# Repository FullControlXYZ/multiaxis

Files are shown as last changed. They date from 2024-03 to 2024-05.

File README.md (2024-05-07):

# multiaxis

### follow **[THIS GUIDANCE DOCUMENT](https://colab.research.google.com/github/FullControlXYZ/multiaxis/blob/main/prusai3_XYZB1/prusa_4axis_guide_colab.ipynb)** to convert a prusa i3 to a 4-axis printer **AND** use [FullControl](https://github.com/FullControlXYZ/fullcontrol/#readme) to generate 4-axis gcode directly within the guide!

A 5-axis addon is described [here](https://github.com/FullControlXYZ/multiaxis/tree/main/prusai3_XYZB1C0#readme)

<p align="center">
  <picture>
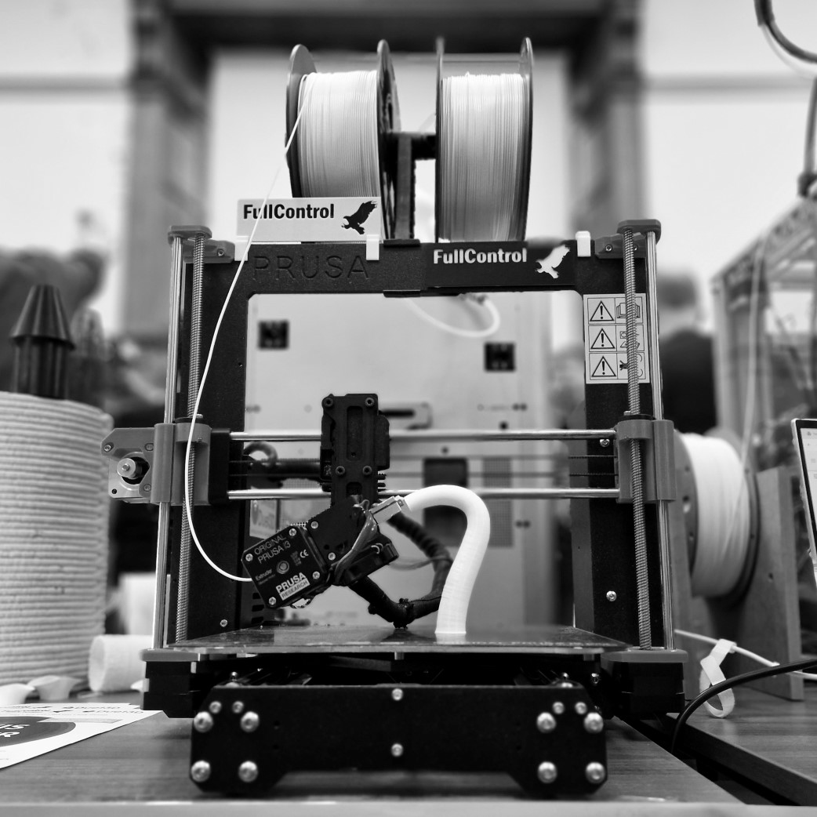
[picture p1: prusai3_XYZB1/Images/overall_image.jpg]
  
  </picture>
  <br><b>think beyond <em>'normal'</em> 3D printing</b><br><br>
</p>

------------------

repo information:

open-source multiaxis 3D printing capabilities developed as part of [FullControl research](https://github.com/FullControlXYZ/fullcontrol/#readme) with support from [Duet3D](https://www.duet3d.com/) and undertaken by engineering students (Renush Vigneswaran and Nathanael Hogg) at [Loughborough University](https://www.lboro.ac.uk/)

if you follow the guide, please let us know :) ... email [info@fullcontrol.xyz](mailto:info@fullcontrol.xyz)

it links to 5-axis and multi-tool revisions of the 4-axis version

multiaxis toolpath design demos are provided in [FullControl documentation](https://github.com/FullControlXYZ/fullcontrol/#readme)

current naming convention (may change in the future):

- X Y Z [i][0/1] [ii][0/1] ...
    - i/ii/... = rotation axes (X=A, Y=B, Z=C)
    - 0/1 indicates whether the stated axis rotates the print-platform/tool respectively
    - axes are listed in the order: X then Y then Z (omit X/Y/Z if not present) then print-platform-rotation axes (0-axes), then tool-rotation axes (1-axes)
        - for multiple directly connected rotation axes, a sequence of parent-child dependency is used: a rotating print-platform (C0) attached onto a tilting stage (A0) would be A0C0 (C is dependent on A)

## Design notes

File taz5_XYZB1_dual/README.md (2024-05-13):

follow the **[PRUSA_i3 GUIDANCE DOCUMENT](https://colab.research.google.com/github/FullControlXYZ/multiaxis/blob/main/prusai3_XYZB1/prusa_4axis_guide_colab.ipynb)** as much as possible

changes from that document:
- print stl files from [here](https://github.com/FullControlXYZ/multiaxis/tree/main/taz5_XYZB1_dual/CAD)
    - (step files are [here](https://github.com/FullControlXYZ/multiaxis/tree/main/taz5_XYZB1_dual/CAD/STEP)) - adjust them for the geometry of the extruders you use
- different re-wiring procedure
    - this [duet wiring doc](https://github.com/FullControlXYZ/multiaxis/tree/main/taz5_XYZB1_dual/Duet%20Wiring) is a useful reference
    - also check duet guidance doc ([example](https://docs.duet3d.com/How_to_guides/e3p_Mini5+_guide_part1_wiring))
- changes to duet configuration files - [updated version available here](https://github.com/FullControlXYZ/multiaxis/tree/main/taz5_XYZB1_dual/Config%20Files)
- an example fullcontrol design is [here](https://colab.research.google.com/github/FullControlXYZ/multiaxis/blob/main/taz5_XYZB1_dual/demo.ipynb)
- we used a [100:1 gearbox-motor combo](https://www.active-robots.com/3322-0-28sth32-nema-11-bipolar-stepper-with-100-1.html?amp=1), more precise than 27:1, but this meant we needed backlash compensation in the toolpath
- anything else? let us know!

email: [info@fullcontrol.xyz](mailto:info@fullcontrol.xyz)

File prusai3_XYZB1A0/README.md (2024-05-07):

guidance for this is upcoming, but it's very simple... 

- follow the [rotating-bed 5-axis guide](https://github.com/FullControlXYZ/multiaxis/tree/main/prusai3_XYZB1C0/#readme)
- reorient the 5th axis so the rotation happens about X instead of Z - good for printing on a mandrel or other parts
- maybe no modifications to config.g (to be confirmed) - all inverse kinematics are handled by FullControl
- change the manual homing routine (set all axes to the zero when the nozzle tip is in line with the mandrel axis, at a logical X)
- change settings used in FullControl for inverse kinematics

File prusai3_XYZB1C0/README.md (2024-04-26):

follow the **[PRUSA_i3 GUIDANCE DOCUMENT](https://colab.research.google.com/github/FullControlXYZ/multiaxis/blob/main/prusai3_XYZB1/prusa_4axis_guide_colab.ipynb)** with the following additions:

- print the additional stl files from [here](https://github.com/FullControlXYZ/multiaxis/tree/main/prusai3_XYZB1C0/CAD)
- wire in the new motor ('C' in this image):
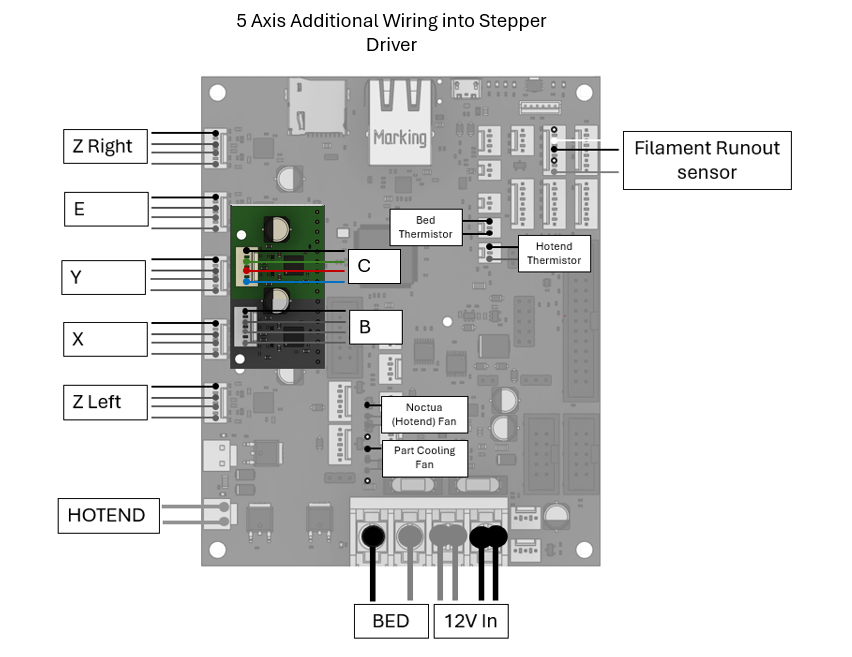
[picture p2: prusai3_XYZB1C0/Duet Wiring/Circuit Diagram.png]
    
- implement minor changes to config file described in the 'Changes to config' section below (updated config file available [here](https://github.com/FullControlXYZ/multiaxis/blob/main/prusai3_XYZB1C0/prusai3_XYZB1C0/Config%20Files/))
- Follow the '5-axis manual homing routine' instructions below
- anything missing from these instructions? let us know! [info@fullcontrol.xyz](mailto:info@fullcontrol.xyz)

## Changes to config:

By utilising the same motor as the 4th axis, the method to add any additional axis in any orientation requires very few changes to config.g:
- Define the extra drive and update the mapping command in the “ ##### Drives” section (changes highlighted in bold): 
    - **M569 P6 S0 D3 V10 		        ; C drive @6**
    - M584 X1 Y2 Z0:4 E3 B5 **C6**                            ; set drive mapping
- Set motor parameters (changes highlighted in bold): 
    - M350 X16 Y16 Z16 E16 B16 **C16** I1  ; configure microstepping with interpolation
    - M92 X100.00 Y100.00 Z400.00 E140.00 B238.6776859 **C238.6776859**    ; set steps per mm 
    - M566 X600.00 Y600.00 Z48.00 E300.00 B480 **C480**      ; set maximum instantaneous speed changes (mm/min)
    - M203 X8000.00 Y8000.00 Z720.00 E7200.00 B5000.00 **C5000.00**    ; set maximum speeds (mm/min)
    - M201 X1250.00 Y1250.00 Z1250.00 E2000.00 B1000.00 **C1000.00** ; set accelerations (mm/s^2)
    - M906 X750 Y750 Z600 E700 B600 **C600** I30                  ; set motor currents (mA) and motor idle factor in per cent
- Update the axis limits:
    - Original (4-axis):
        - M208 X0:200 Y0:210 Z0:200 B-90:90             ; set axis minima and maxima
    - Updated:
        - **M208 X-100:100 Y-105:105 Z-50:40 B-90:90 C-999999:999999**             ; set axis minima and maxima

## 5-axis manual homing routine:

Manually home axes (to be automated in the future):
1. Place 5th axis motor bracket on the print bed :
    - Whilst this could be anywhere on the print bed, depending on the design, it is recommended to leave at centre (The axes limits have been set assuming central position)

1. Home B:
    - Use Duet Web Control to jog B until nozzle points directly down 

1. Position Nozzle to be at the centre of the rotating bed (an indentation is designed into bed to clearly indicate centre):
    - Use Duet Web Control to jog X, Y and Z until the nozzle pinches paper at the centre of the bed.
    - Note down X Y (anmd maybe Z) values to easily move to this position for subsequent homing.

1.	Set home for all axis: G92 Z0 X0 Y0 B0 C0 

1. Begin printing, following these steps:
    1.	Click T0 in duet web control and set nozzle temperature and bed temperature
    1.	Load gcode file (without start/end-procedures except M82/M83) onto printer
    1.	Run gcode file (use very slow speeds if you have no cooling fan)

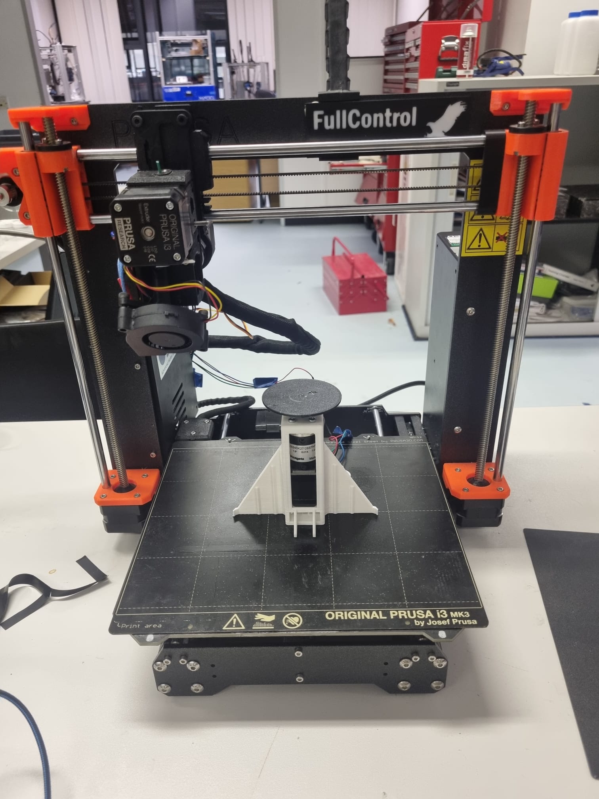
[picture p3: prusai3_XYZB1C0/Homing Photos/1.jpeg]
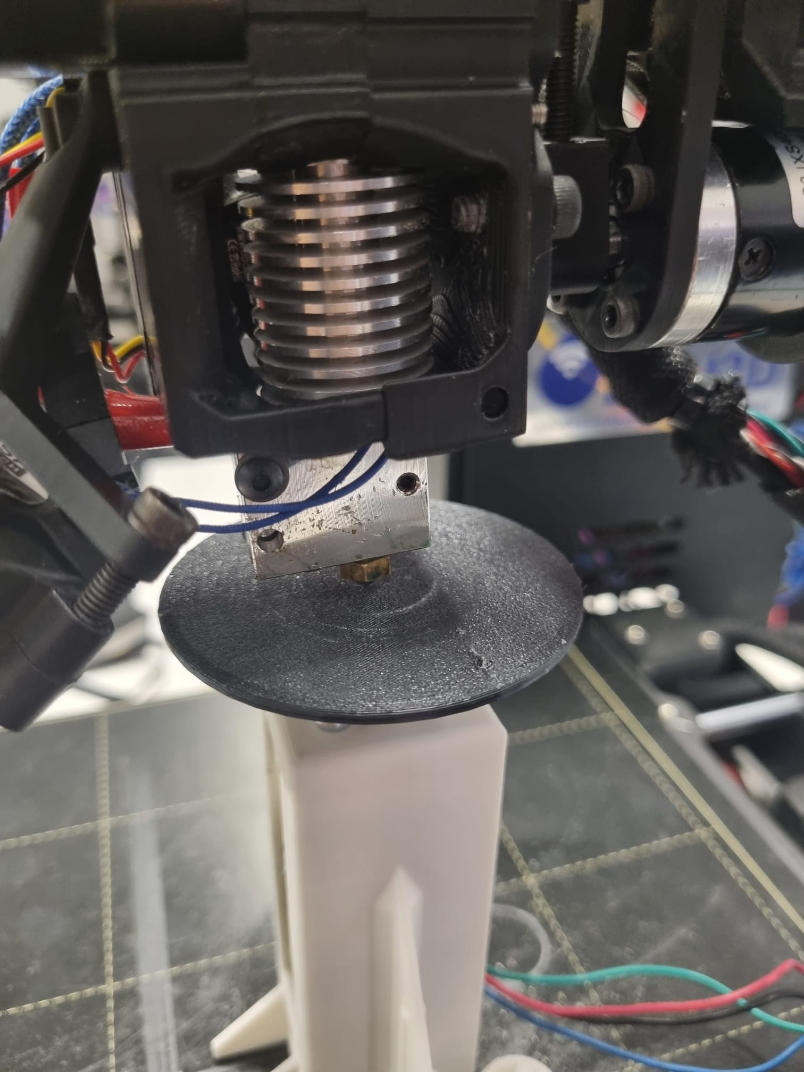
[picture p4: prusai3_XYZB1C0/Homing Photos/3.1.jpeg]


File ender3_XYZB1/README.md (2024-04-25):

follow the **[PRUSA_i3 GUIDANCE DOCUMENT](https://colab.research.google.com/github/FullControlXYZ/multiaxis/blob/main/prusai3_XYZB1/prusa_4axis_guide_colab.ipynb)** as much as possible

changes from that document:
- print stl files from [here](https://github.com/FullControlXYZ/multiaxis/tree/main/ender3_XYZB1/CAD) instead of the three prusa brackets
    - these are untested and may need minor modifications (step files are [here](https://github.com/FullControlXYZ/multiaxis/tree/main/ender3_XYZB1/CAD/STEP)) - please give feedback and help develop this work!
- you no longer need the Duet 3 Mini 2+ expansion board since there is only one Z-axis motor (it is required for the prusa because it has two Z motors)
    - note: you may wish to use one anyway, to be able to update to 5-axis in the future
- minor changes to wiring
    - this [ender 3 pro guidance doc](https://docs.duet3d.com/How_to_guides/e3p_Mini5+_guide_part1_wiring) may be a useful reference
- minor changes to config file (only one motor for Z axis)
- anything else? let us know!

email: [info@fullcontrol.xyz](mailto:info@fullcontrol.xyz)

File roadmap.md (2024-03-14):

immediate:
1. add endstops and automated homing guidance
1. add part cooling guidance
    1. options: existing fan / aquarium pump
1. add brackets for alternative printers
1. add a 5th axis (rotating bed and mandrel options)
1. turret tool!!! (multiple print heads and inspection tools 'activated' simply by rotation of the B axis)

maybe:
1. remove bracket supporting the back of the motor by increasing rigity of the front bracket
1. try a [more widely available](https://thepihut.com/products/bipolar-stepper-motor-with-planet-gear-box-18kg-cm) motor-gearbox combo but lower gear ratio (is microstepping enough?)

next:
1. templates/guides for community contribution
1. further demos and docs for automated 4- and 5-axis toolpath generation with FullControl
    - combine with stl import... still not 'slicing' but using geometric data in a range of ways
1. conversions that can utilise the existing controller board for printers
1. conversions of non-bed-slinger printers

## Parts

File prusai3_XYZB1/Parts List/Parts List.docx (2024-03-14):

Parts | Quantity | Source
Nema 11 Stepper Motor with 27:1 Gearbox | x1 | https://www.active-robots.com/3321-0-28sth32-nema-11-bipolar-stepper-with-27-1-gearbox.html
Duet 3 Mini 5+ | X1 | https://www.duet3d.com/duet3mini5plus
Duet 3 mini 2+ | X1 | https://www.duet3d.com/duet3expansionmini2plus
Extruder Bracket | X1 | Print STL files available here: https://github.com/FullControlXYZ/media/tree/main/4_axis_docs/CAD
Motor Bracket Front | X1
Motor Bracket Rear | X1
Duet Case | X1
Duet Case Lid | X1
Hotend Cover | X1 - Optional
M3x10 | X11
M3 Nut | X1
M4x10 | X6
M4x40 | X2
M4x25 | X1
M4x6 | X1

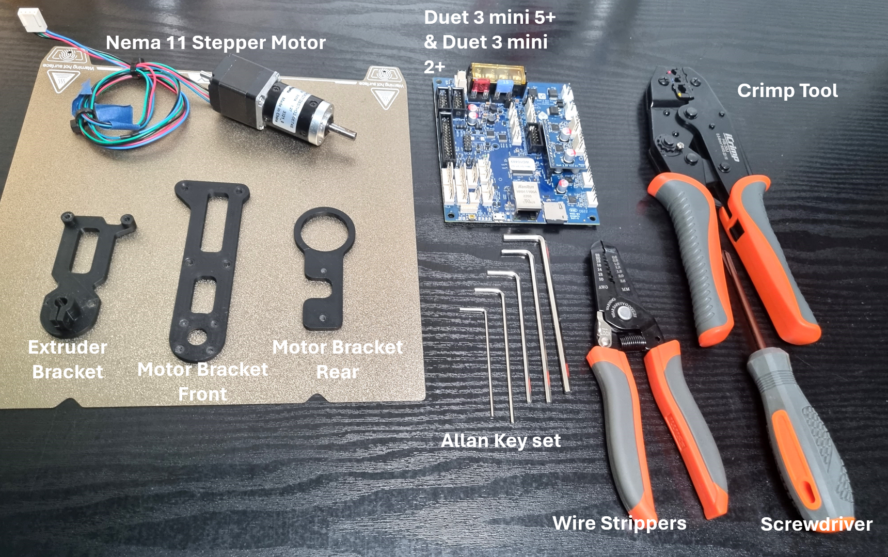
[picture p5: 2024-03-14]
prusai3_XYZB1/Parts List/Basic Parts.png

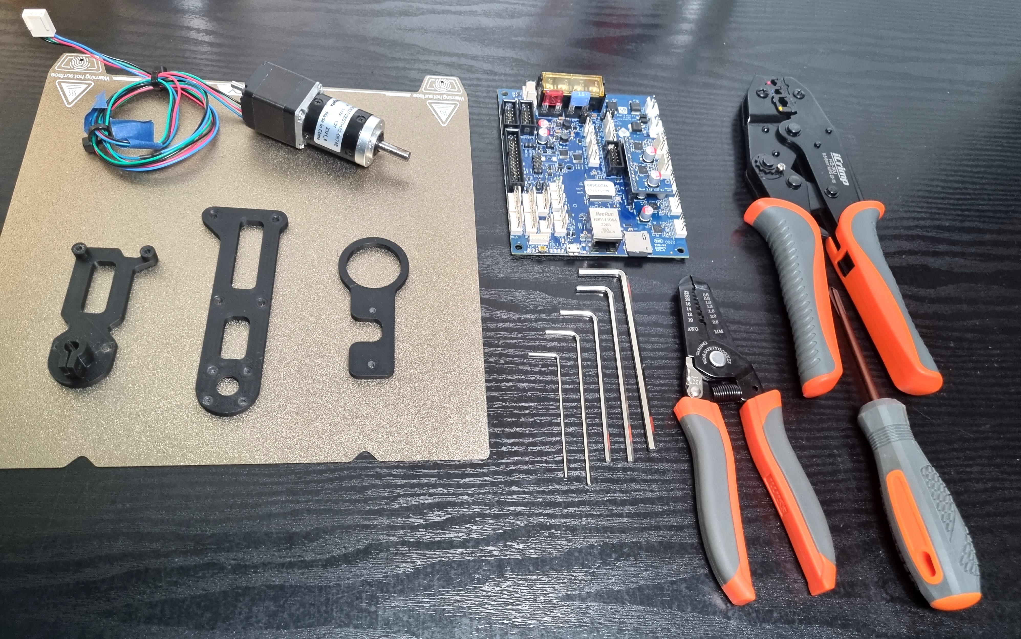
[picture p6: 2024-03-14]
prusai3_XYZB1/Parts List/Parts Image.jpg

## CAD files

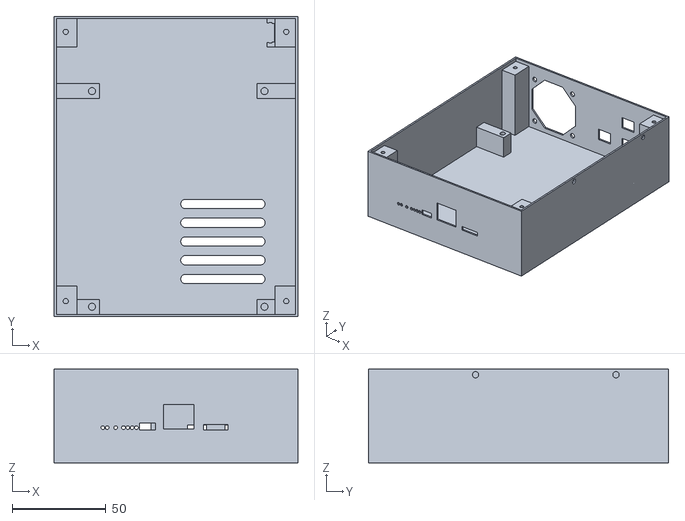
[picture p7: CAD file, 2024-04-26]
prusai3_XYZB1/CAD/Optional/Duet Case.stl
130.0 x 160.0 x 50.0

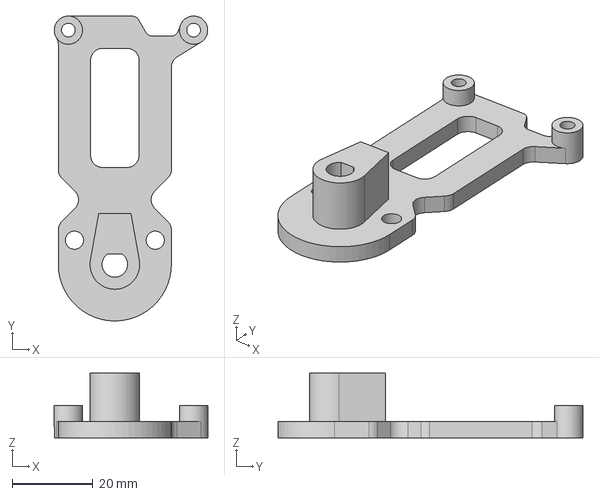
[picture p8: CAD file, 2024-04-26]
prusai3_XYZB1/CAD/step/Extruder Bracket.step
38.0 x 75.5 x 16.0 mm

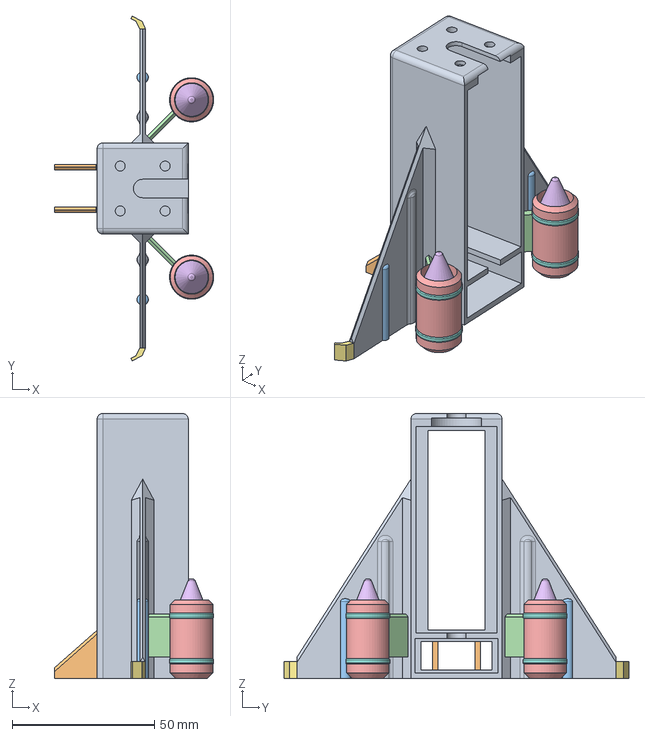
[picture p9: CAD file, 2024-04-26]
prusai3_XYZB1C0/CAD/STEP/Motor Bracket.stp
55.9 x 121.0 x 93.0 mm

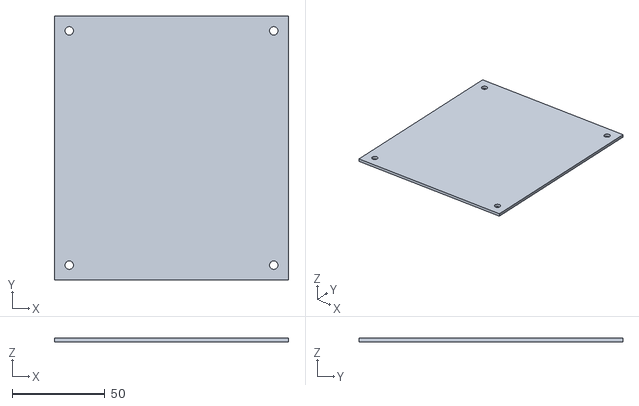
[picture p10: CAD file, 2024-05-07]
taz5_XYZB1_dual/CAD/DuetEnclosureLid.stl
126.0 x 142.0 x 2.00

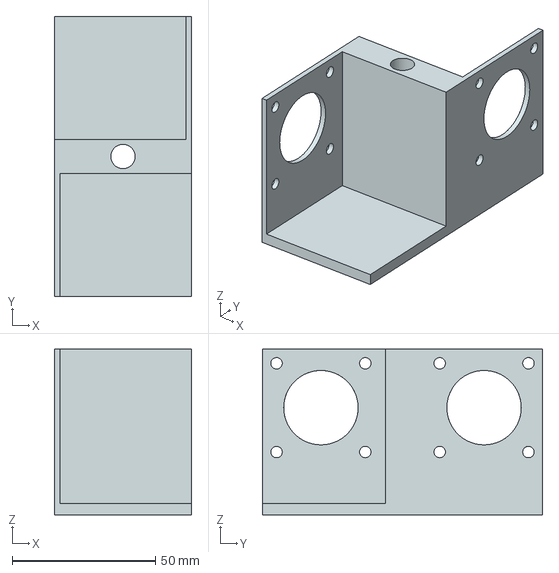
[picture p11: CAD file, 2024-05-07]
taz5_XYZB1_dual/CAD/Step/ExtruderMount.stp
48.0 x 98.0 x 58.0 mm

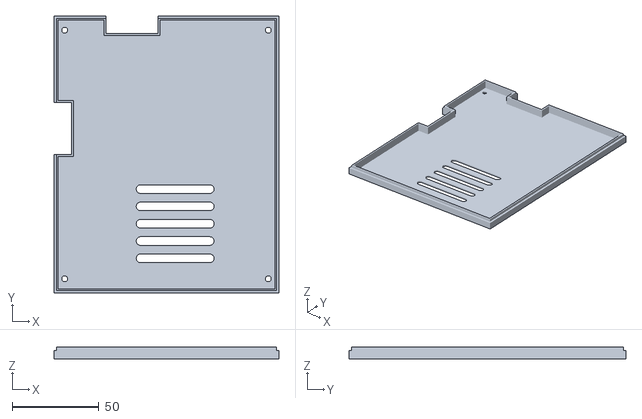
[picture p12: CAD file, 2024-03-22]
prusai3_XYZB1/CAD/Optional/Duet Case Lid.stl
130.0 x 160.0 x 6.99

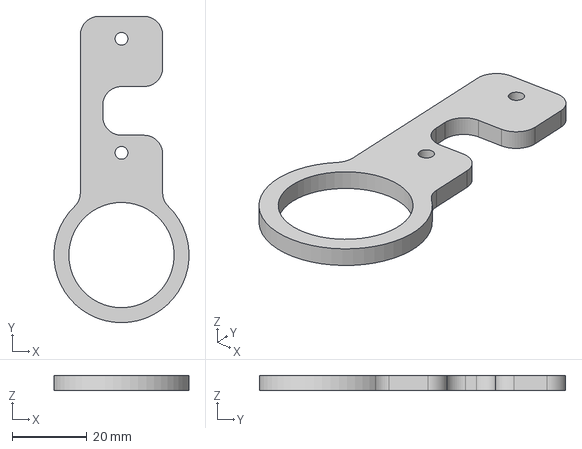
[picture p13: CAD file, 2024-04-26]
prusai3_XYZB1/CAD/step/Motor Bracket Rear.step
36.0 x 81.8 x 4.00 mm

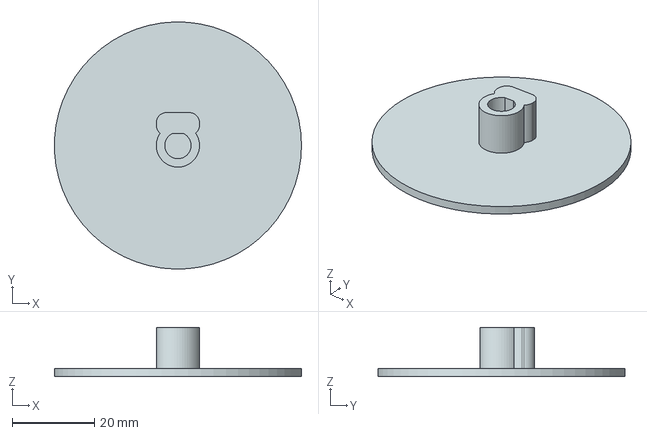
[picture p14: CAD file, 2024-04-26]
prusai3_XYZB1C0/CAD/STEP/Rotating Bed.stp
60.0 x 60.0 x 12.0 mm

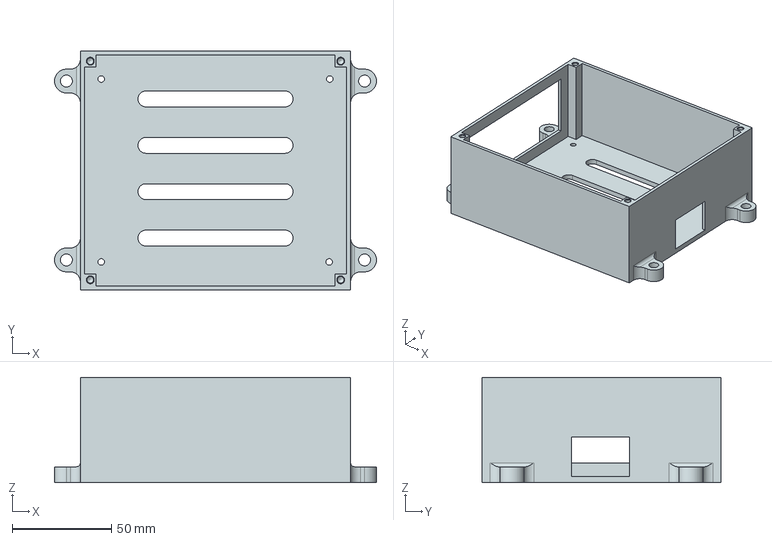
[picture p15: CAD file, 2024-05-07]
taz5_XYZB1_dual/CAD/Step/DuetEnclosure.stp
162.0 x 120.0 x 53.0 mm

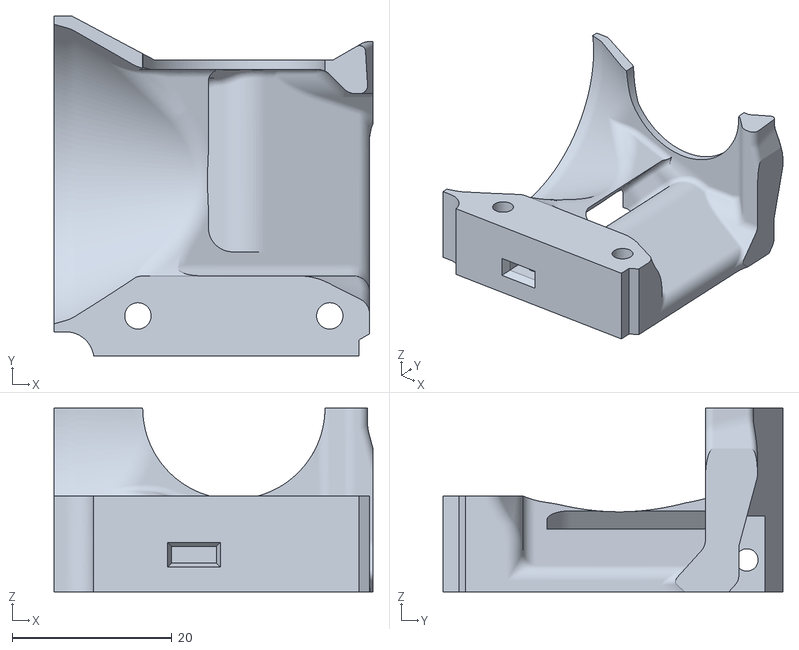
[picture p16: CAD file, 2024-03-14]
prusai3_XYZB1/CAD/Optional/Hotend Cover.stl
39.9 x 42.5 x 23.0

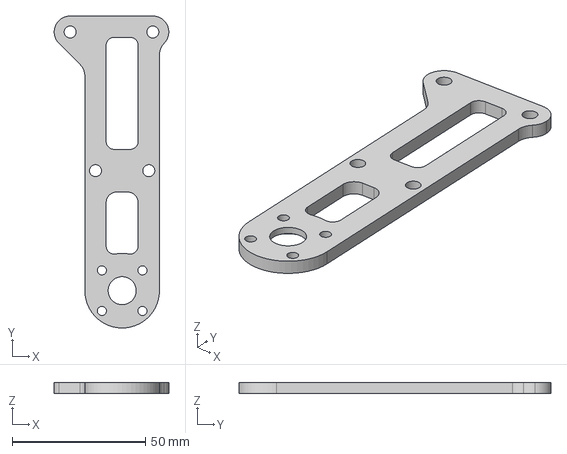
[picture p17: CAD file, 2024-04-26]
prusai3_XYZB1/CAD/step/Motor Bracket Front.step
43.0 x 117.0 x 4.00 mm

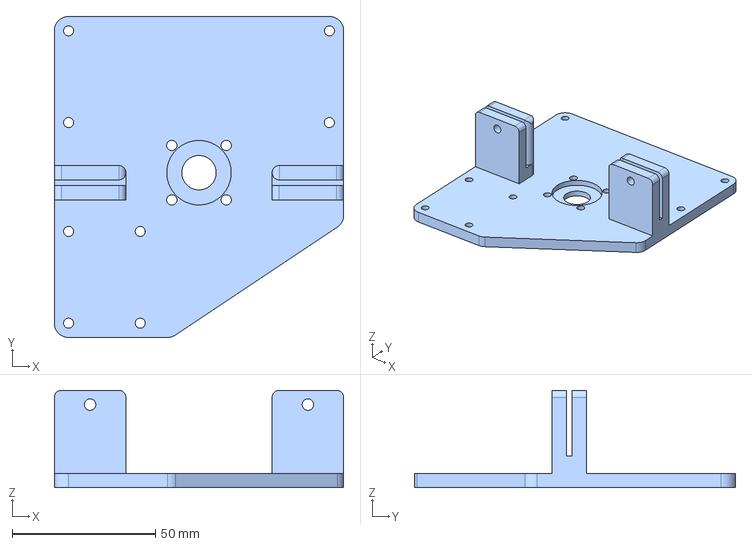
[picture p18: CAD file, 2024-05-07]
taz5_XYZB1_dual/CAD/Step/Backplate.stp
101.0 x 112.0 x 34.0 mm

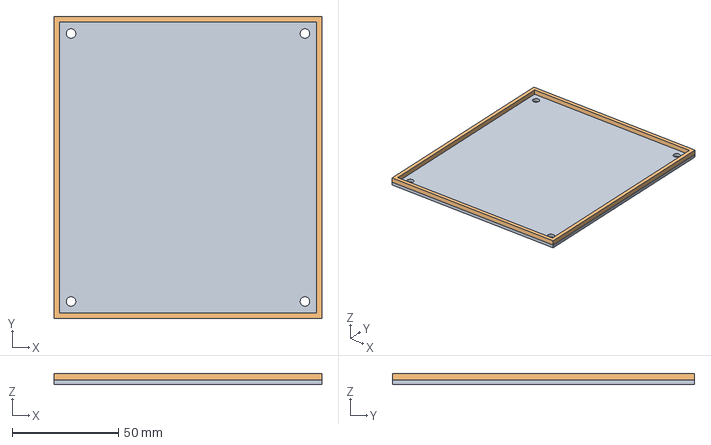
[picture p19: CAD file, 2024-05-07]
taz5_XYZB1_dual/CAD/Step/DuetEnclosureLid.prt.stp
126.0 x 142.0 x 5.00 mm

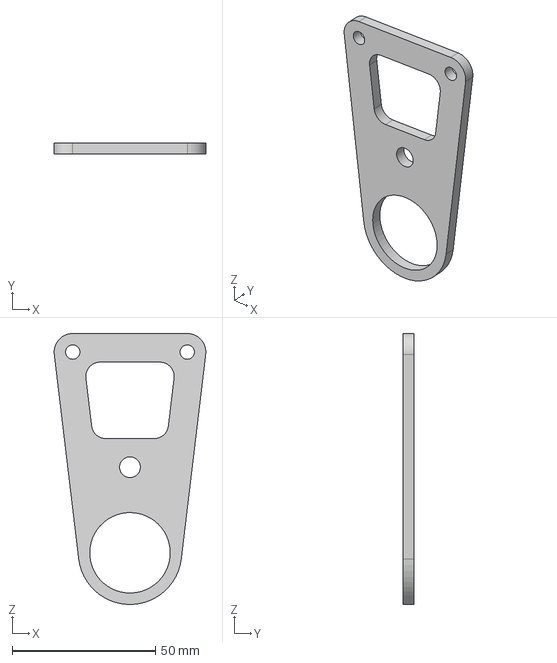
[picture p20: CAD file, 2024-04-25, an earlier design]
ender3_XYZB1/CAD/STEP/Motor Bracket Rear.step
53.0 x 4.00 x 94.7 mm

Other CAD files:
prusai3_XYZB1/CAD/Old/Motor Bracket Rear v01.stl
ender3_XYZB1/CAD/STEP/Motor Bracket Front.step
prusai3_XYZB1/CAD/Old/Extruder Bracket v01.stl
ender3_XYZB1/CAD/STEP/Extruder Bracket.step
ender3_XYZB1/CAD/Extruder Bracket.stl
ender3_XYZB1/CAD/Motor Bracket Front.stl
ender3_XYZB1/CAD/Motor Bracket Rear.stl
prusai3_XYZB1/CAD/Extruder Bracket.stl
prusai3_XYZB1/CAD/Motor Bracket Front.stl
prusai3_XYZB1/CAD/Motor Bracket Rear.stl
prusai3_XYZB1/CAD/Old/Motor Bracket Front v01.stl
prusai3_XYZB1C0/CAD/STL/Motor Bracket.stl
prusai3_XYZB1C0/CAD/STL/Rotating Bed.stl
taz5_XYZB1_dual/CAD/Backplate.stl
taz5_XYZB1_dual/CAD/DuetEnclosure.stl
taz5_XYZB1_dual/CAD/ExtruderMount.stl

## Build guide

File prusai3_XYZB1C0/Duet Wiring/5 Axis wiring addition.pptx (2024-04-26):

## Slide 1

5 Axis Additional Wiring into Stepper Driver

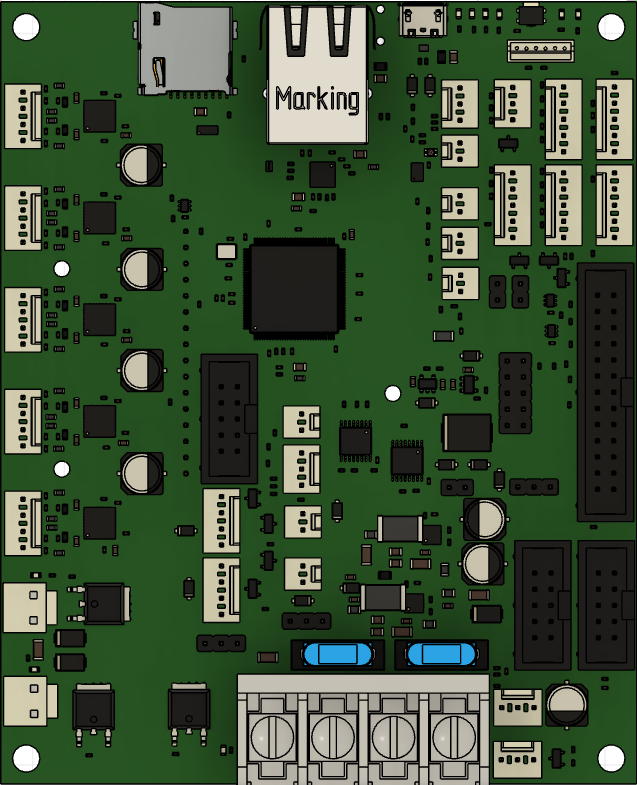
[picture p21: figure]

Z Right

Filament Runout sensor

E

Y

Bed Thermistor

Hotend Thermistor

X

Z Left

HOTEND

BED

12V In

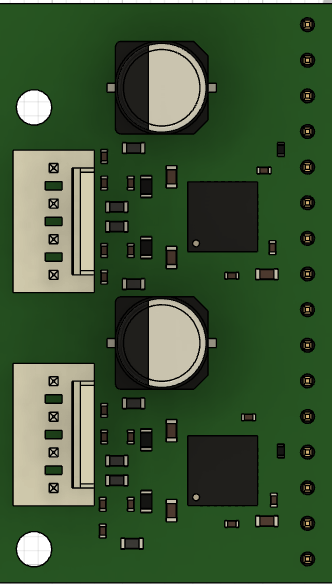
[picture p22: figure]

B

C

Noctua (Hotend) Fan

Part Cooling Fan

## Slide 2

5 Axis Additional Wiring into Stepper Driver

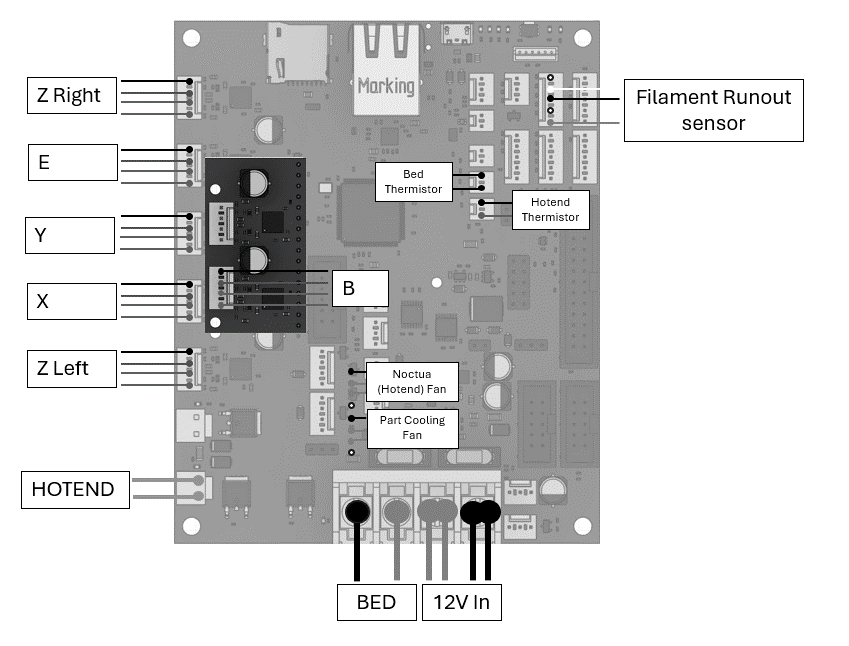
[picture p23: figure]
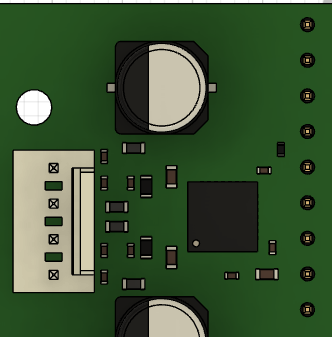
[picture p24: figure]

C

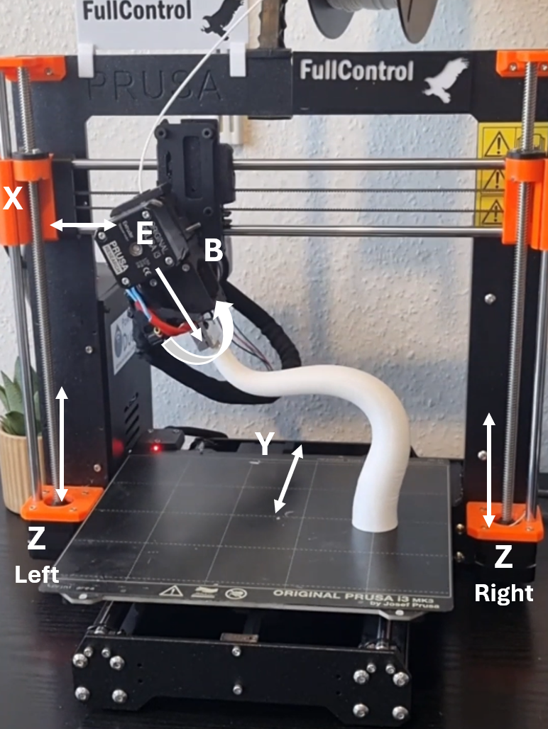
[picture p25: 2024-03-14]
prusai3_XYZB1/Images/Printer Axis Labelled.png

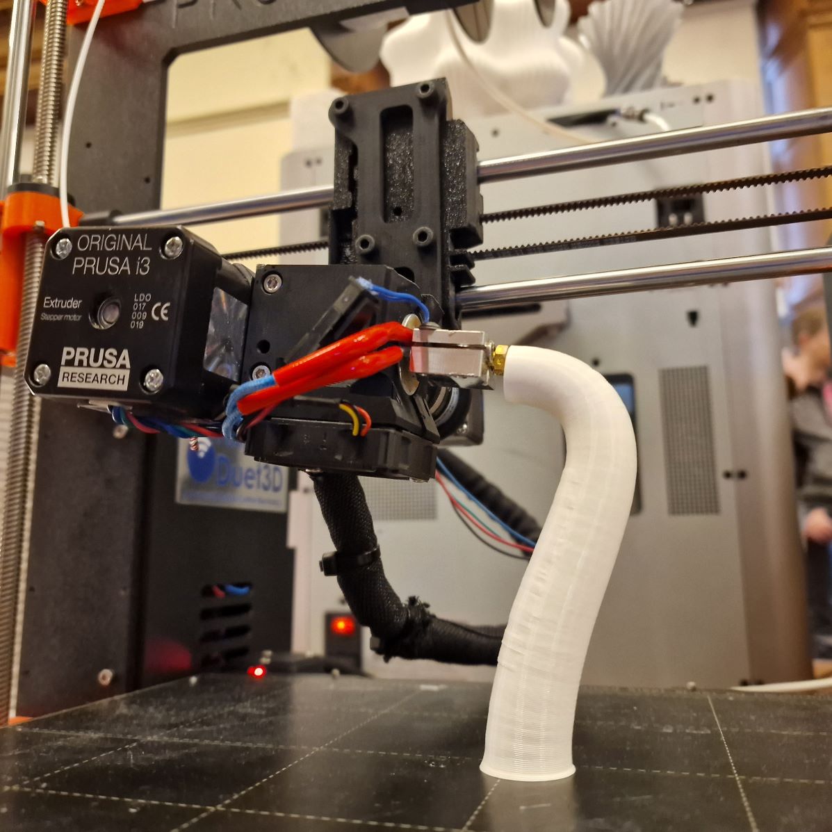
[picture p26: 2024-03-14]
prusai3_XYZB1/Images/zoomed_printing_image.jpg

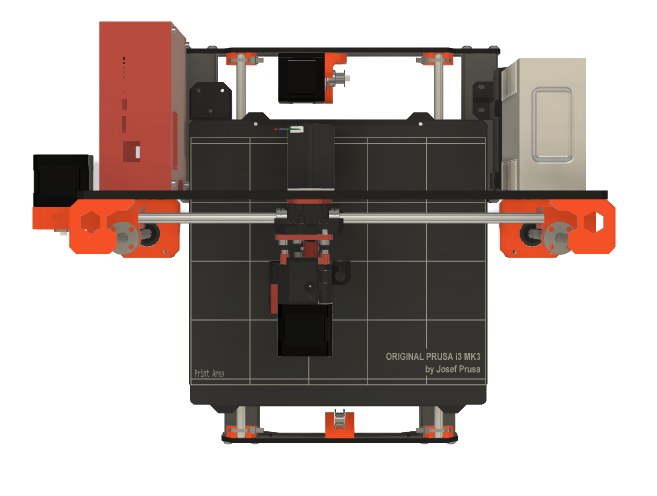
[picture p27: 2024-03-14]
prusai3_XYZB1/Exploded View/Assembled Birdseye View.png

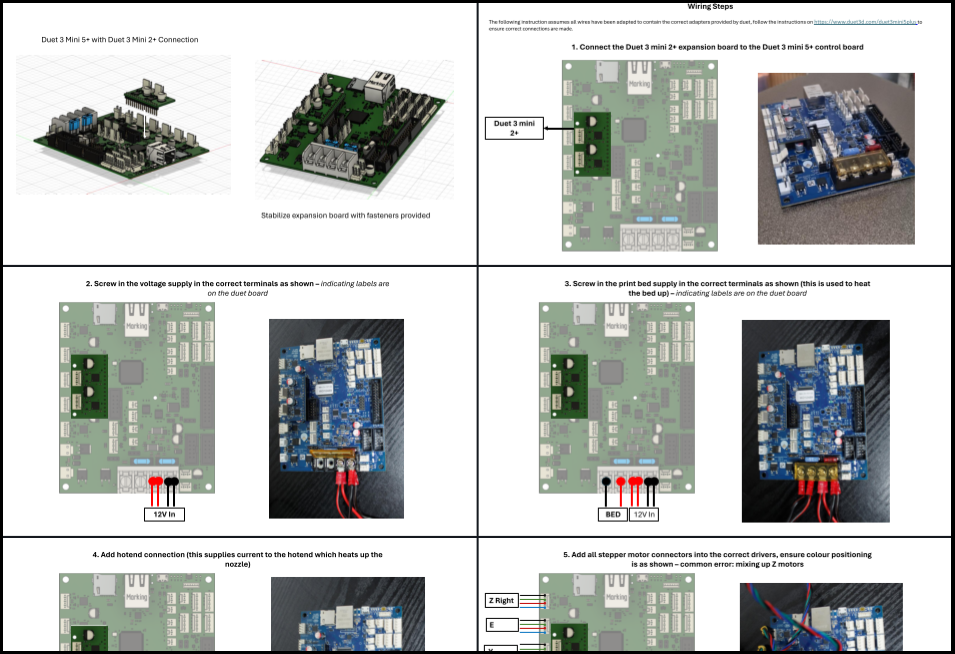
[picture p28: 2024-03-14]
prusai3_XYZB1/Duet Wiring/Screenshot.png

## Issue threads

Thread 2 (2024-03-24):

Adding a new rotary axis!

Fisherm2, 2024-03-24:
I am very interested in your 4-axis printer, I would like to make a similar 5-axis printer, and the difference with your project is that I try to add two rotary axes in the print head, is there any related firmware support or tutorial document, thank you very much!

fullcontrol-xyz, 2024-03-30:
This isn't something I've previously done but it will be supported by FullControl! And the firmware will handle it easily as long as FullControl (or some equivalent software) does the inverse kinematics. Let us know when you are close to a working system and we can get the kinematics sorted out if it isn't already built in to FullControl by that time. Sorry for the slow reply... I accidently didn't have notifications set up for this repo 🤦

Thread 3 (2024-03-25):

Motor Bracket Front Hole Alignment Issue

NealParkhurst, 2024-03-25:
Firstly, huge congrats on a fabulous project!

When assembling the Motor Bracket Front to the gearbox I found that it was tricky to get the fixing holes lined up and was concerned that I might cross thread / damage the threads. As the gearbox is already concentrically aligned by the step detail in the bracket you could increase the diameter of the fixing thru holes to eliminate this issue. Cheers, Neal

fullcontrol-xyz, 2024-03-30:
Thanks very much for letting us know. Sorry for the slow reply. I didn't have alerts set on for issues for some reason. We'll sorting out larger holes. We're also working on some slightly updated brackets. So will make sure they feature in them

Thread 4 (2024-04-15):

3d printers compatibility

Prumnea, 2024-04-15:
I have read your work on converting the Prusa MK3S to have a 4th-axis printer. That is really impressive!
 I would like to ask if other types of Prusa printers or printers from other brands would work as well?

Regards,
Prumnea

fullcontrol-xyz, 2024-04-15:
Thanks very much!

Yep it will work in basically an identical manner for any other printer that you convert to run off the duet controller.

There may be some small changes to the firmware required (e.g. if there is only one motor for the z axis instead of two), but if there are any changes required, they will be minor and you can ask on here for help.

There will also potentially need to be some changes to the brackets. I'm not sure how the x-carriages vary from prusa to prusa. This would involve designing a revised bracket with new hole positions. It's an easy CAD job. We've provided the step files for our models.

We're already looking at releasing brackets for an ender 3. If anyone creates new brackets for alternative printers, please let us know and we'll add them to this repo and the guide so other people can benefit!

Andy

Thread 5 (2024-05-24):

Using an alternative controller board

fullcontrol-xyz, 2024-05-24:
Questions by email:

Hello, I am currently following your mod for the 4th axis for the prusa and I have few questions.
1. any board that works on reprap with more than 6 steppers should work? XY2ZEB considering that the board I am thinking to use is having 7 steppers, i am currently can't get my hands on the duet mini 5+ because it is really expensive to get in my country, and importing it myself will be expensive as well.
2. there is any alternative for the nema11 with gearbox? as far I understand you want to use nema11 for it light weight uses and the gearbox to get higher torque?
I can't somehow get my hands on it and thought maybe I could get my hands on different one?
I can order this from amazon but it will take well over a month to arrive.
3. at the demo design I really didn't understand what is the "Nozzle_Tip_axis_offset" mean if you could have a simple explanation for this is will be great.
4. Can I get the whole step files for the project with the printer included? In case I would want to fit stuff to it on the github there is a step only for the printed parts.
And thank you again for your amazing work, can't wait to start building this.

fullcontrol-xyz, 2024-05-24:
Response:

That’s really cool to hear you’re following the instructions.
In response to your questions:
1.	It should yes, but you’ll need to modify the firmware yourself (please share your firmware and board details if you do! – we’ll add it to the github repo)
2.	You can try an alternative gearbox/motor for sure. We got a 100:1 gearbox version of the one we link to (27:1) and it worked, but introduced backlash, for which we needed to compensate in FullControl. So I’d go for a gear ratio of perhaps 10-50 and see how it goes. Weight is the main consideration yeh.
3.	Nozzle tip axis offset is the distance the nozzle is below the axis of rotation (B axis). This is important because when rotate the toolhead, the distance of the nozzle tip from the axis of rotation dictates how much the nozzle moves.
4.	I’ll ask my student to send the printer step files.

AssafKatan, 2024-05-24:
Hello, thank you for answer!
This is assaf Whom sent the email.
1. I got my self a Mellow E3 RRF board, it does have enough stepper drivers to work with 4 axis for now this will be enough, I will consider getting a duet board if there will be an integration of 5th axis by you guys or rather by me if I will find it possible.(Considering the price of the duet boards this was a easy buy for me just to test the concept).

2. I found myself a motor that will fit the original design, I could find a seller on aliexpress that sold me a nema11 27:1 motor that should just fit in the design, if not I will make some changes to make it fit.

I have got myself a Prusa clone just beacuse I thought that assembling it on a original prusa is hurtful lol, considering they are pretty expensive in my country and I could find the clone for less than a half price so it will be good for testing this.
I will update in this thread about my work using the different board.

3-4 Thank you!! this is really helpful, and releasing this project as open source is amazing and I am really happy about it, I am 7 years into printing and always wanted to try more than the normal "2.5D" printing.

fullcontrol-xyz, 2024-06-03:
All sounds good! Let us know any progress, if you need to make changes to any of the brackets keep good records along with any other necessary deviations from the guidance doc. Then we'll be able to quickly write a custom guide for your printer and controller, which only states what needs to be done differently to the original guidance. The idea is that eventually, there may be 100s of different printer and controllers, but only a single guide, with infinite possible minor variations of it.

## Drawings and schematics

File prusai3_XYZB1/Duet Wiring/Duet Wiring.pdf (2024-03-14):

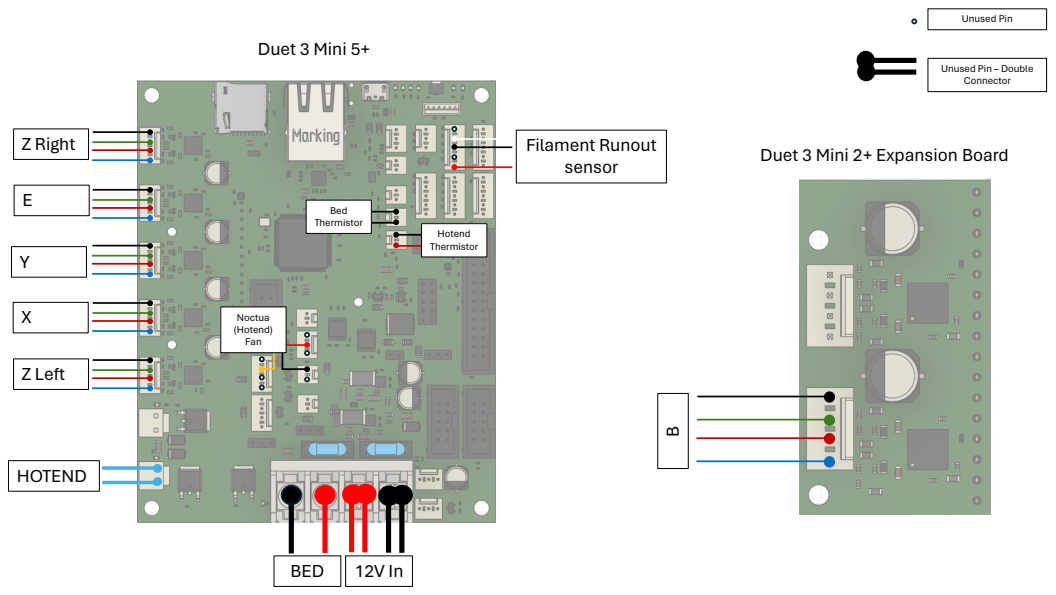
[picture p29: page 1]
Z Right; Z Left; HOTEND; BED; Filament Runout sensor; Noctua (Hotend) Fan; Bed Thermistor; Hotend Thermistor; Unused Pin; Duet 3 Mini 5+

Unused Pin – Double
Connector

Duet 3 Mini 2+ Expansion Board

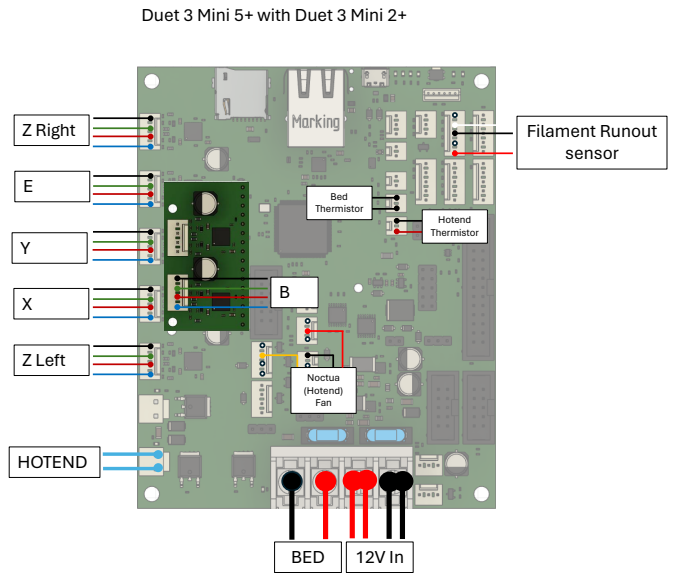
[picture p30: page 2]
Z Right; Z Left; HOTEND; BED; Filament Runout sensor; Noctua (Hotend) Fan; Bed Thermistor; Hotend Thermistor

Duet 3 Mini 5+ with Duet 3 Mini 2+

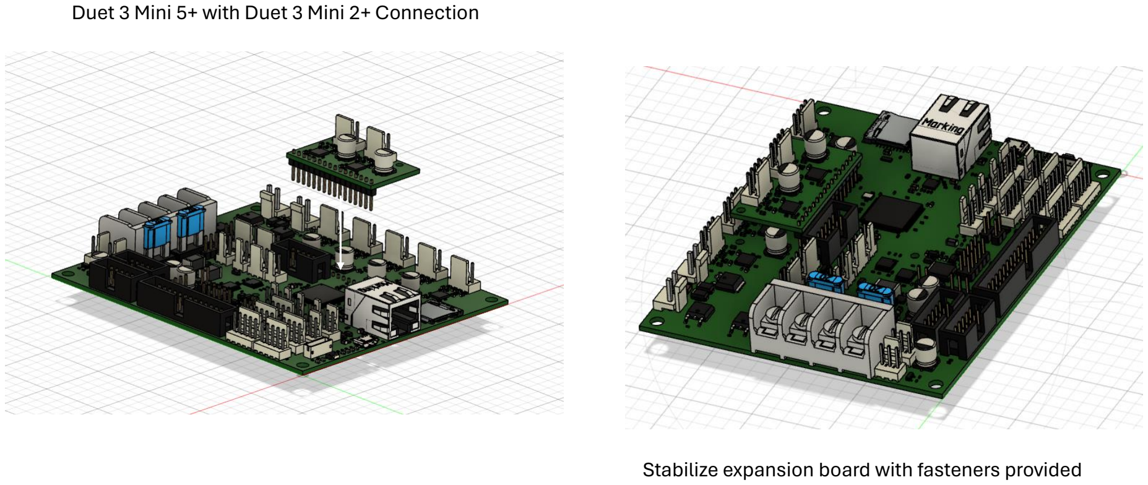
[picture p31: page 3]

Duet 3 Mini 5+ with Duet 3 Mini 2+ Connection

Stabilize expansion board with fasteners provided

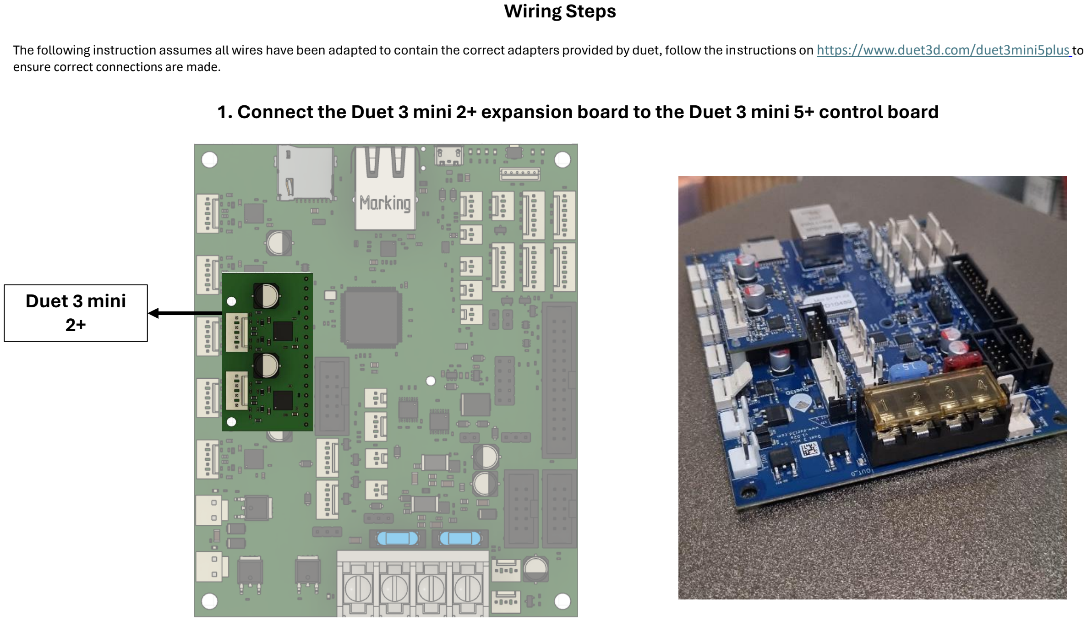
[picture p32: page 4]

Wiring Steps

### 1. Connect the Duet 3 mini 2+ expansion board to the Duet 3 mini 5+ control board

The following instruction assumes all wires have been adapted to contain the correct adapters provided by duet, follow the instructions on https://www.duet3d.com/duet3mini5plusto
ensure correct connections are made.

Duet 3 mini
2+

### 2. Screw in the voltage supply in the correct terminals as shown – indicating labels are

on the duet board

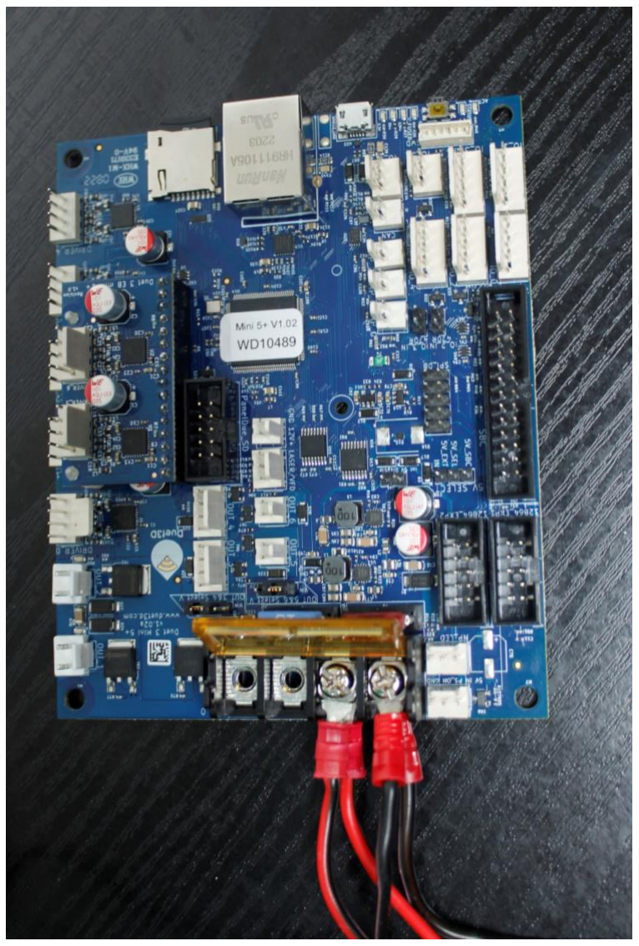
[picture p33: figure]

12V In

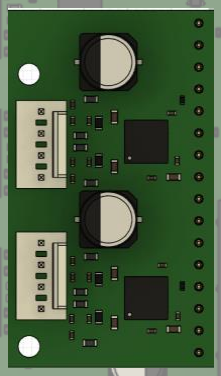
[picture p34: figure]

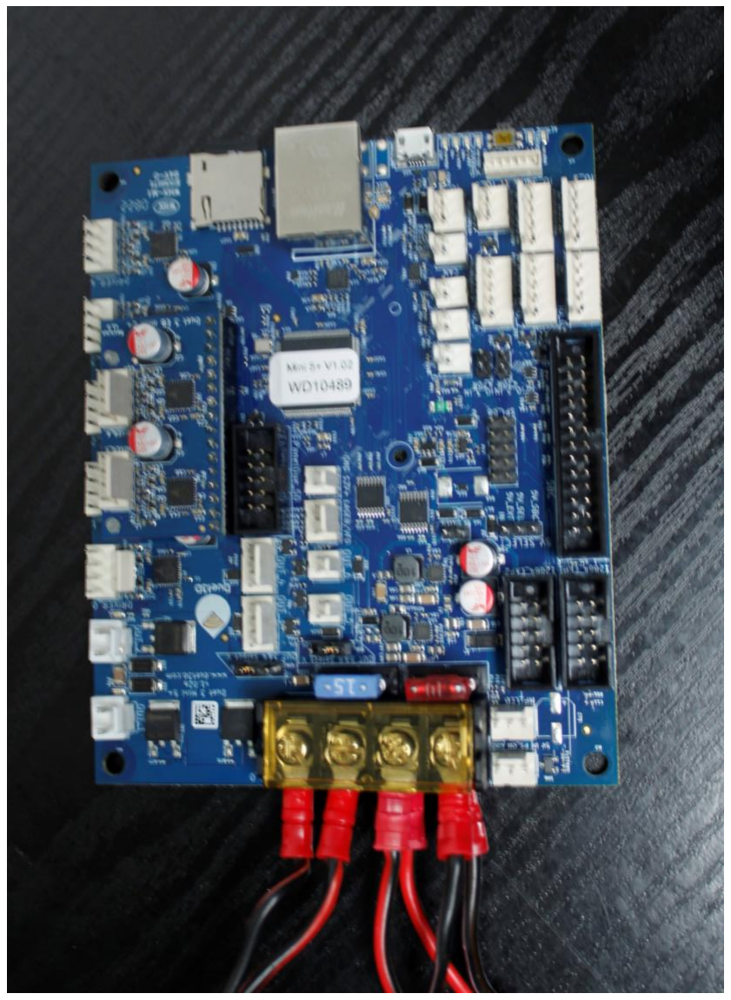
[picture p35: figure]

BED 12V In

### 3. Screw in the print bed supply in the correct terminals as shown (this is used to heat

the bed up) – indicating labels are on the duet board

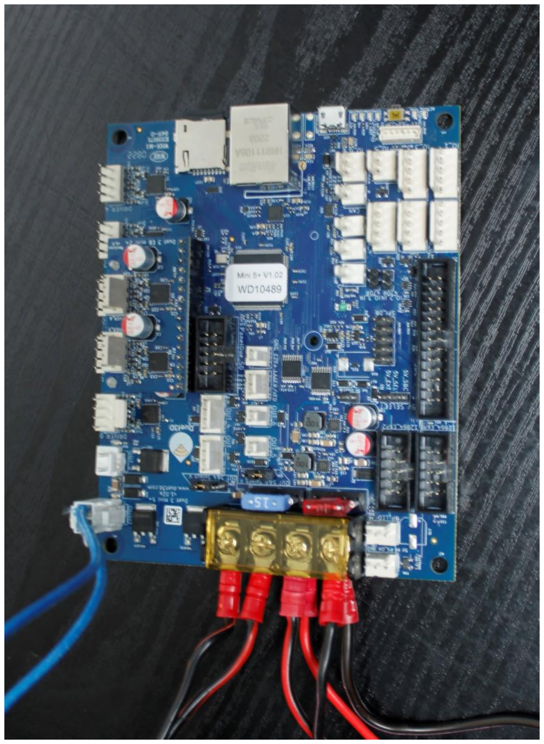
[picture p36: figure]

HOTEND

BED 12V In

### 4. Add hotend connection (this supplies current to the hotend which heats up the

nozzle)

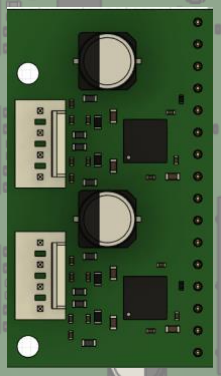
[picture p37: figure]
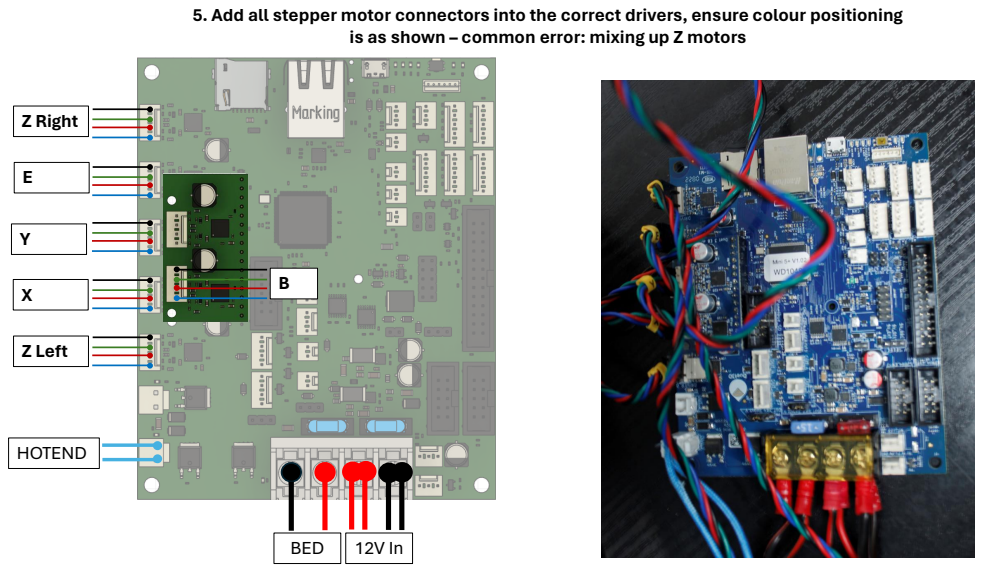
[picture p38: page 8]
Z Right; Z Left; HOTEND; BED

5. Add all stepper motor connectors into the correct drivers, ensure colour positioning

is as shown – common error: mixing up Z motors

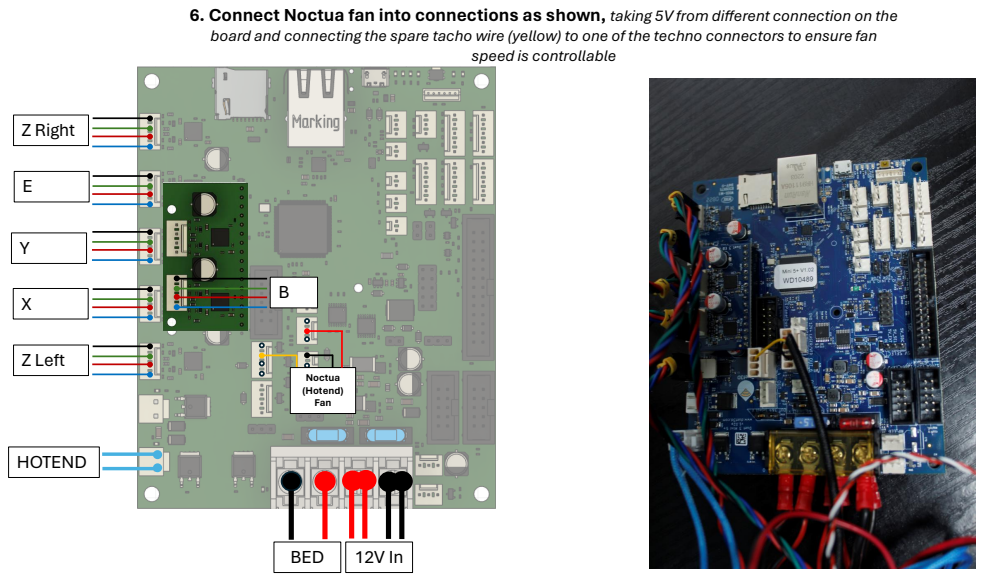
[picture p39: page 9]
Z Right; Z Left; HOTEND; BED; Noctua (Hotend) Fan

6. Connect Noctua fan into connections as shown, taking 5V from different connection on the
board and connecting the spare tacho wire (yellow) to one of the techno connectors to ensure fan

speed is controllable

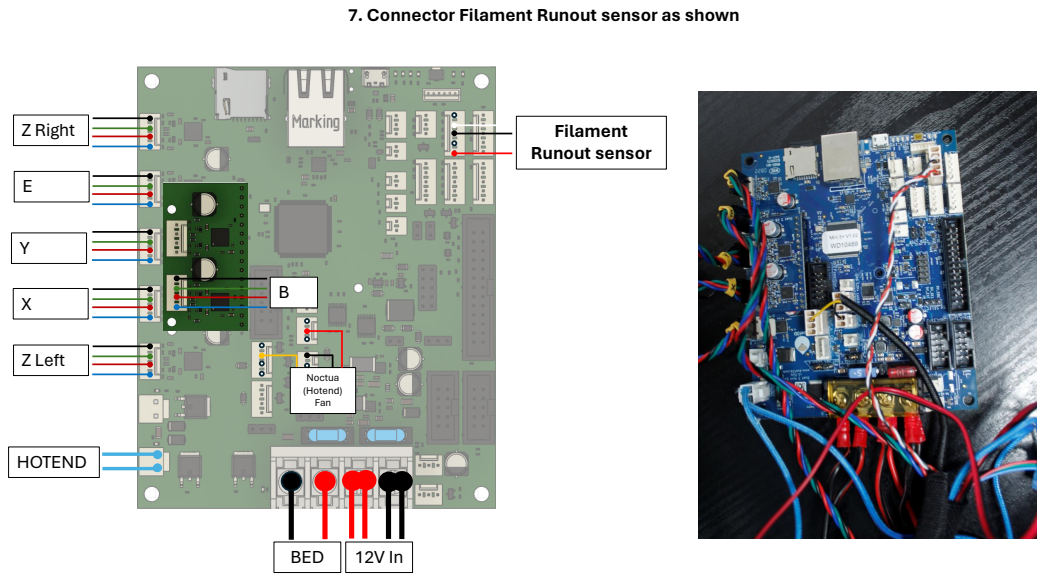
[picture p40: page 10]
Z Right; Z Left; HOTEND; BED; Filament Runout sensor; Noctua (Hotend) Fan

7. Connector Filament Runout sensor as shown

Z Right; Z Left; HOTEND; BED; Filament Runout sensor; Noctua (Hotend) Fan; Bed Thermistor; Hotend Thermistor

8. Connect Bed thermistor and hotend thermistor as shown

Wiring is Complete

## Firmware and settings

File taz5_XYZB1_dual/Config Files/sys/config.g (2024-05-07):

; Configuration file for Duet 3 Mini 5+ (firmware version 3.3)
; executed by the firmware on start-up
;
; generated by RepRapFirmware Configuration Tool v3.3.16 on Tue Nov 28 2023 13:41:44 GMT+0000 (Greenwich Mean Time)

; General preferences
M575 P1 S1 B57600                                  ; enable support for PanelDue
G90                                                ; send absolute coordinates...
M83                                                ; ...but relative extruder moves
M550 P"LulzBot"                                    ; set printer name
M918 P1 E4 F2000000                                ; configure direct-connect display

; Network
M552 P192.168.2.6 S1                               ; enable network and set IP address
M553 P255.255.255.0                                ; set netmask
M554 P192.168.1.254                                ; set gateway
M586 P0 S1                                         ; enable HTTP
M586 P1 S0                                         ; disable FTP
M586 P2 S0                                         ; disable Telnet

; Drives
M569 P0 S0 D3 V10
M569 P1 S1 D3 V10                                        ; physical drive 0.1 goes backwards X
M569 P2 S1 D3 V100                                      ; physical drive 0.2 goes forwards	Z
M569 P3 S1 D3 V100									
M569 P4 S0 D3 V10                                      ; C
M569 P5 S0 D3 V0
M569 P6 S0 D3 V0
M584 X1 Y0 Z2:3 B4 E5:6                         ; set drive mapping
M350 X16 Y16 Z16 B16 E16:16 I1                            ; configure microstepping with interpolation

M92 X100.00 Y100.00 Z1600.00 B880 E833:860                ; set steps per mm
M566 X900.00 Y900.00 Z60.00 B500.00 E300:300                ; set maximum instantaneous speed changes (mm/min)
M203 X6000.00 Y6000.00 Z600.00 B10000.00 E7200:7200         ; set maximum speeds (mm/min)
M201 X500.00 Y500.00 Z200.00 B5000.00 E2000:E2000                ; set accelerations (mm/s^2)
M906 X800 Y800 Z800 B670 E700:700 I30                       ; set motor currents (mA) and motor idle factor in per cent
M84 S30                                            ; Set idle timeout

; Axis Limits
M208 X0 Y0 Z0 B-360 S1                                   ; set axis minima
M208 X300 Y300 Z300 B360 S0                             ; set axis maxima
M564 H0

; Endstops
M574 X1 S1 P"!io5.in"                               ; configure switch-type (e.g. microswitch) endstop for low end on X via pin io5.in
M574 Y1 S1 P"!io6.in"                               ; configure switch-type (e.g. microswitch) endstop for low end on Y via pin io6.in
M574 Z1 S1 P"!io3.in"                               ; configure switch-type (e.g. microswitch) endstop for low end on Z via pin io2.in

; Z-Probe
M558 P0 H5 F120 T6000                              ; disable Z probe but set dive height, probe speed and travel speed
M557 X5:190 Y5:195 S10                             ; define mesh grid

; Heaters
; Bed Heater
M308 S0 P"temp0" Y"thermistor" B4725 C7.060000e-8 	; configure sensor 0 as thermistor on pin temp1
M950 H0 C"out0" Q25 T0                              ; create bed heater output on out0 and map it to sensor 0, PWMfrequency: 25Hz
M307 H0 R0.262 C338.0 D10.52 S1.00 V11.8 B0			; Bed tuning values, enable PID
M140 H0                                                    	; Bed uses Heater 0
M143 H0 S120                                               ; Set temperature limit for heater 0 to 120C Bed

; Hotend heater 1 (E)
M308 S1 P"temp1" Y"thermistor" B4725 C7.060000e-8 			; configure sensor 1 as thermistor on pin temp0
M950 H1 C"out1" T1                           				; create nozzle heater output on out1 and map it to sensor 1
M307 H1 B0 S1.00                             				; disable bang-bang mode for heater  and set PWM limit
M143 H1 S230                                 				; set temperature limit for heater 1 to 295C
M302 S170 R50                                        			; allow extrusion starting from 170°C and retractions already from 170°C

; Hotend heater 2 (N)
M308 S2 P"temp2" Y"thermistor" B4725 C7.060000e-8
M950 H2 C"out2" T2
M307 H2 B0 S1.00
M143 H2 S230
M302 S170 R50


; Fans
; Hotend cooling fan (1) E
M950 F1 C"out5" Q5000							; NOCTUA fan an pin out6 with 5000Hz PWM frequency
M106 P1 T35 S255 H1  							; Temperature control: turn fan on at 55°C

; Tools
; Hotend cooling fan (2) N
M950 F2 C"out6" Q5000							; NOCTUA fan an pin out6 with 5000Hz PWM frequency
M106 P2 T35 S255 H2  							; Temperature control: turn fan on at 55°C

M563 P0 S"T0" D0 H1 F1   ; define tool 0 (Hotend heater 1)
G10 P0 X0 Y0 Z0 B0 ; set tool 0 axis offsets
G10 P0 R0 S0 

M563 P1 S"T1" D1 H2 F2   ; define tool 1 (Hotend heater 2)
G10 P1 X0 Y0 Z0 B0 ; set tool 1 axis offsets
G10 P1 R0 S0 

M572 D0 S0.06


; Custom settings are not defined

M18 X Y Z B E 

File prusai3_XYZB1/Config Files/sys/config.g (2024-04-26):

; Configuration file for Duet 3 Mini 5+ (firmware version 3.3)
; executed by the firmware on start-up
;
; generated by RepRapFirmware Configuration Tool v3.3.16 on Fri Nov 17 2023 19:59:21 GMT+0000 (Greenwich Mean Time)

; General preferences
G90                                                   ; send absolute coordinates...
M83                                                   ; ...but relative extruder moves
M550 P"PrusaMK3S_Duet"                                ; set printer name

; Network
M552 P192.168.2.4 S1                                  ; enable network and set IP address
M553 P255.255.255.0                                   ; set netmask
M554 P192.168.1.254                                   ; set gateway
M586 P0 S1                                            ; enable HTTP
M586 P1 S0                                            ; disable FTP
M586 P2 S0                                            ; disable Telnet

; ##### Drives
M569 P1 S0 D3 V10                                    ; X drive @1
M569 P2 S1 D3 V10                                    ; Y drive @2
M569 P0 S0 D3 V100                                   ; Z left drive @0
M569 P4 S0 D3 V100                                   ; Z right drive  @4
M569 P3 S1 D3 V0                                     ; E drive @3 - inversed
M569 P5 S0 D3 V10                                    ; B drive @5
M584 X1 Y2 Z0:4 E3 B5                               ; set drive mapping
M671 X-37:287 Y0:0 S10                              ; define dual driven z-axis 

M350 X16 Y16 Z16 E16 B16 I1                         ; configure microstepping with interpolation
M92 X100.00 Y100.00 Z400.00 E140.00 B238.6776859    ; set steps per mm - Real steps per degree = 14.91735537, multiply by 16 for microstepping (238.6776859) ...FOR REF: 241.3296602
M566 X600.00 Y600.00 Z48.00 E300.00 B480       ; set maximum instantaneous speed changes (mm/min)
M203 X8000.00 Y8000.00 Z720.00 E7200.00 B5000.00    ; set maximum speeds (mm/min)
M201 X1250.00 Y1250.00 Z1250.00 E2000.00 B1000.00  ; set accelerations (mm/s^2)
M906 X750 Y750 Z600 E700 B600 I30                  ; set motor currents (mA) and motor idle factor in per cent
M84 S30                                              ; Set idle timeout
                             						; Set idle timeout
M208 X0:200 Y0:210 Z0:200 B-90:90             ; set axis minima and maxima
M564 H0


; Endstops and stall sensitivity
M574 X1 S3 									; configure sensorless endstop for low end on X
M915 X S3 F0 H400 R1		                ; Set X axis Sensitivity
M574 Y1 S3 									; configure sensorless endstop for low end on Y
M915 Y S3 F0 H400 R1		                ; Set y axis Sensitivity
M574 Z1 S2                                  ; configure Z-probe endstop for low end on Z



; ##### Z-Probe Settings for PINDA 2
M558 P5 C"io2.in" I1 H1 F1000 T6000 A3              				; Prusa PindaV2 Endstop
M308 S2 P"temp2" A"Pinda V2" Y"thermistor" T100000 B3950      		; Prusa PindaV2 Thermistor
G31 P1000 X23 Y5 Z1.4 S21 H2 T0.02                         			; Nozzle offset - Powder Coated Sheet with temperature compensation (0.02mm/°C)
;G31 P1000 X23 Y5 Z1.1 S21 H2 T0.02                                    			; Nozzle offset - Smooth Sheet
M574 Z1 S2                                                 			; Set Z axis endstop, controlled by probe
M557 X24:228 Y6:210 P5                                    			; Define mesh grid for probing
M376 H5																; Fade height 5mm

; Heaters

M308 S0 P"temp1" Y"thermistor" B4725 C7.060000e-8 					; configure sensor 0 as thermistor on pin temp1
M950 H0 C"out0" Q25 T0                           					; create bed heater output on out0 and map it to sensor 0, PWM frequency: 25Hz
M307 H0 R0.262 C338.0 D10.52 S1.00 V11.8 B0							; Bed tuning values, enable PID
M140 H0                                                    			; Bed uses Heater 0
M143 H0 S120                                               			; Set temperature limit for heater 0 to 120C Bed

M308 S1 P"temp0" Y"thermistor" T100000 B4725 C7.06e-8 ; configure sensor 1 as thermistor on pin temp0
M950 H1 C"out1" T1                                    ; create nozzle heater output on out1 and map it to sensor 1
M307 H1 B0 S1.00                                      ; disable bang-bang mode for heater  and set PWM limit
M143 H1 S295                                          ; set temperature limit for heater 1 to 295C

; Fans
; Hotend cooling fan
M950 F0 C"out6" Q5000												; NOCTUA fan an pin out6 with 5000Hz PWM frequency
M106 P0 T55 S255 H1  												; Temperature control: turn fan on at 55°C

; Tools
M563 P0 D0 H1 F-1                                     ; define tool 0
G10 P0 X0 Y0 Z0                                       ; set tool 0 axis offsets
G10 P0 R0 S0                                          ; set initial tool 0 active and standby temperatures to 0C

; Custom settings are not defined

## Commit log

2024-03-14 initial version
    [Duet Case Lid.stl, Duet Case.stl, Extruder Bracket.stl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]
2024-03-22 replaced incorrect stl file with correct one
    [Duet Case.stl]
2024-03-28 New and old CAD
    [Duet Case Lid.stl, Duet Case.stl, Extruder Bracket.stl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]
2024-03-28 Rename Extruder Bracket.stl to Extruder Bracket v01.stl
    [Extruder Bracket v01.stl]
2024-03-28 Rename Motor Bracket Front.stl to Motor Bracket Front v01.stl
    [Motor Bracket Front v01.stl]
2024-03-28 Rename Motor Bracket Rear.stl to Motor Bracket Rear v01.stl
    [Motor Bracket Rear v01.stl]
2024-03-28 Rename Duet Case Lid.stl to Duet Case Lid v01.stl
    [Duet Case Lid v01.stl]
2024-03-28 Rename Duet Case.stl to Duet Case v01.stl
    [Duet Case v01.stl]
2024-03-28 Rename Hotend Cover.stl to Hotend Cover v01.stl
    [Hotend Cover v01.stl]
2024-03-28 New and old CAD files
    [Duet Case Lid v01.stl, Duet Case Lid.stl, Duet Case v01.stl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]
2024-04-12 Rename to match original
    [Extruder Bracket.stl]
2024-04-25 ender3 4-axis added
    [Extruder Bracket.step, Extruder Bracket.stl, Motor Bracket Front.step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]
2024-04-26 5-axis update
    [Motor Bracket.stl, Motor Bracket.stp, Rotating Bed.stl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]
2024-05-07 taz dual-extruder option added
    [Backplate.stl, Backplate.stp, DuetEnclosure.stl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]
2024-05-07 taz dual-extruder corrections
